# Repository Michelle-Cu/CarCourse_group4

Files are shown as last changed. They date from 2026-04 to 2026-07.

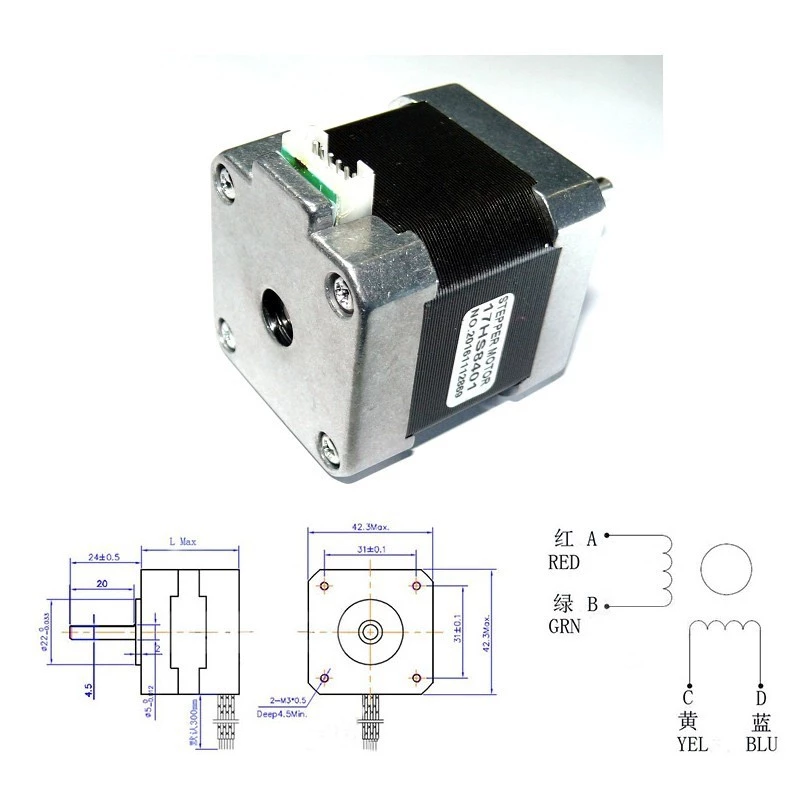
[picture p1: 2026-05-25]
SelfChosenTopic/Carinventor/Nema17圖紙.webp

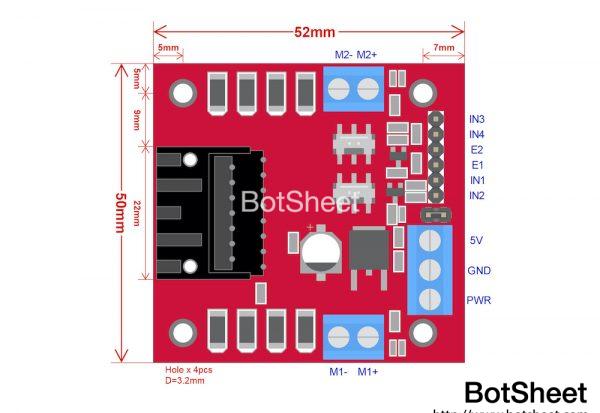
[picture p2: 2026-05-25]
SelfChosenTopic/Carinventor/l298n-motor-driver-module-dimension-600x413.jpeg

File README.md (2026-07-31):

# CarCourse_group4

## Results

Finger movements:
Robotic finger bends according to the flex sensors on the glove.
Finger movements

Punch:
Robotic arm ejects when the sensor glove's acceleration exceeds 1.5g.
Punch

Demo Video:
https://www.youtube.com/watch?v=hl6YXo5eNV0

## Project structure:

```mermaid
flowchart TB
    %% ==================== 手套端 (GLOVE SIDE) ====================
    subgraph GLOVE ["手套端感測 (Glove Controller)"]
        direction TB
        A["使用者手部動作"] --> B1["自製彎曲感測器 ×5<br/>(手指彎曲)"]
        A --> B2["MPU6050 加速度感測器<br/>(手腕姿態與速度)"]

        subgraph Flex_Proc ["手指訊號處理"]
            C1["讀取類比電壓值"] --> D1["Kalman Filter"]
            D1 --> E1["三段式角度校正"]
            E1 --> F1["映射至機器手指角度<br/>(0° ~ 180°)"]
        end

        subgraph Acc_Proc ["寸拳判定邏輯"]
            C2["讀取三軸加速度"] --> D2["計算運動加速度<br/>√(x² + y² + z²)"]
            D2 --> E2{"加速度<br/>> 1.5g (15 m/s²)?"}
            E2 -- 是 --> F2_1["設置出拳旗標 (Punch Flag = 1)"]
            E2 -- 否 --> F2_2["設置出拳旗標 (Punch Flag = 0)"]
        end

        B1 --> C1
        B2 --> C2

        F1 --> G1["資料整合與封包打包<br/>(PACKED Struct)"]
        F2_1 --> G1
        F2_2 --> G1
    end

    %% ==================== 通訊與接收 (COMMUNICATION) ====================
    G1 --->|ESP-NOW 無線通訊<br/> 6-Byte packet| H1["ESP32 接收端"]

    %% ==================== 接收端主控邏輯 (MAIN LOGIC) ====================
    subgraph MAIN_SYSTEM ["機械手臂"]
	    H1
    end

    %% ==================== 三維輸出端 (ROBOTIC HAND / ARM / AUDIO) ====================
    subgraph PALM_SYS ["手掌端 (Robotic Hand)"]
        H1 ----> K1["伺服馬達角度映射<br/>(硬體極限安全調校)"]
        K1 --> L1["寫入 5× Servo Motors"]
        L1 --> M1["驅動機械手指仿生運動"]
    end

    subgraph ARM_SYS ["手臂寸拳端 (Robotic Arm)"]
        H1 ----> K2{"出拳 flag == 1<br/>且 未處於出拳狀態<br/>且 冷卻時間 > 1秒?"}
        K2 -- 是 --> L2_1["點亮指示 LED &<br/>驅動步進馬達正轉 90°<br/>【寸拳強力彈出】"]
        K2 -- 否 --> L2_2["步進馬達保持靜態阻尼"]
        
        L2_1 --> M2_1["手臂恢復 <br/>(延遲 1 秒)"]
        M2_1 --> M2_2["驅動步進馬達正轉 270°"]
        M2_2 --> M2_3["關閉 LED &<br/>重啟 1秒冷卻計時器"]
        M2_3 --> L2_2
        
        L2_1 -.->|中斷驅動| N2["Hardware Timer ISR<br/>(高精密運動規劃)"]
        M2_2 -.->|中斷驅動| N2
        N2 --> O2["驅動 Stepper Motor"]
    end

    subgraph AUDIO_SYS ["音效端 (Audio System)"]
        H1 ----> K3["寸拳與動作動態音效觸發"]
        K3 --> L3["DFPlayer Mini 模組"]
        L3 --> M3["喇叭即時音效輸出"]
    end

    %% ==================== 視覺樣式設定 (THEMING) ====================
    style GLOVE fill:#e1f5fe,stroke:#03a9f4,stroke-width:2px,color:#000;
    style MAIN_SYSTEM fill:#fff9c4,stroke:#fbc02d,stroke-width:2px,color:#000;
    style PALM_SYS fill:#e8f5e9,stroke:#4caf50,stroke-width:2px,color:#000;
    style ARM_SYS fill:#ffe0b2,stroke:#fb8c00,stroke-width:2px,color:#000;
    style AUDIO_SYS fill:#f3e5f5,stroke:#9c27b0,stroke-width:2px,color:#000;
    
    style E2 fill:#ffe0b2,stroke:#fb8c00,stroke-width:2px,color:#000;
    style K2 fill:#ffe0b2,stroke:#fb8c00,stroke-width:2px,color:#000;
    style H1 fill:#3f51b5,stroke:#303f9f,color:#fff;
    style G1 fill:#03a9f4,stroke:#0288d1,color:#fff;
```

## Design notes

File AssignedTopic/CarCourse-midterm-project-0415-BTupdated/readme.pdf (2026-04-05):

# 電資工程入門設計與實作

# sample code講解

影片連結:https://www.youtube.com/watch?v=WLR578UgFHk

Author: B07901029陳君輔

Contact: chunfuchen0311@gmail.com

Date: 2022/07

# 檔案架構

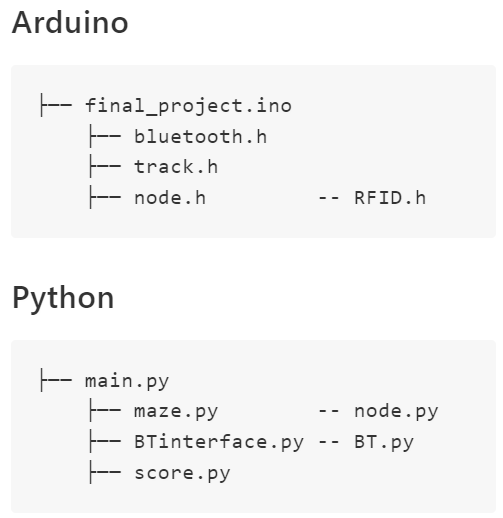
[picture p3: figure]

# Python

## Python 套件安裝

- pip install python-socketio

## score.py使用方法

- ScoreboardFake
- 使用fakeUID.csv裡的資料計分
- 使用時機: server尚未開啟 或者 server太多人在使用
- 分數不會出現在server上
- Scoreboard
- 連線到server計分 (網址以助教公布的為準)
- 使用時機: 想刷榜 或者 正式考試時
- 分數會出現在server上

除了一開始宣告的名字不一
樣之外，其他funtion使用起
來都一樣，可以無痛切換

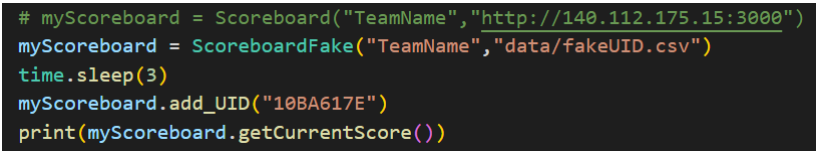
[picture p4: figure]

# Arduino

# 藍芽腳位

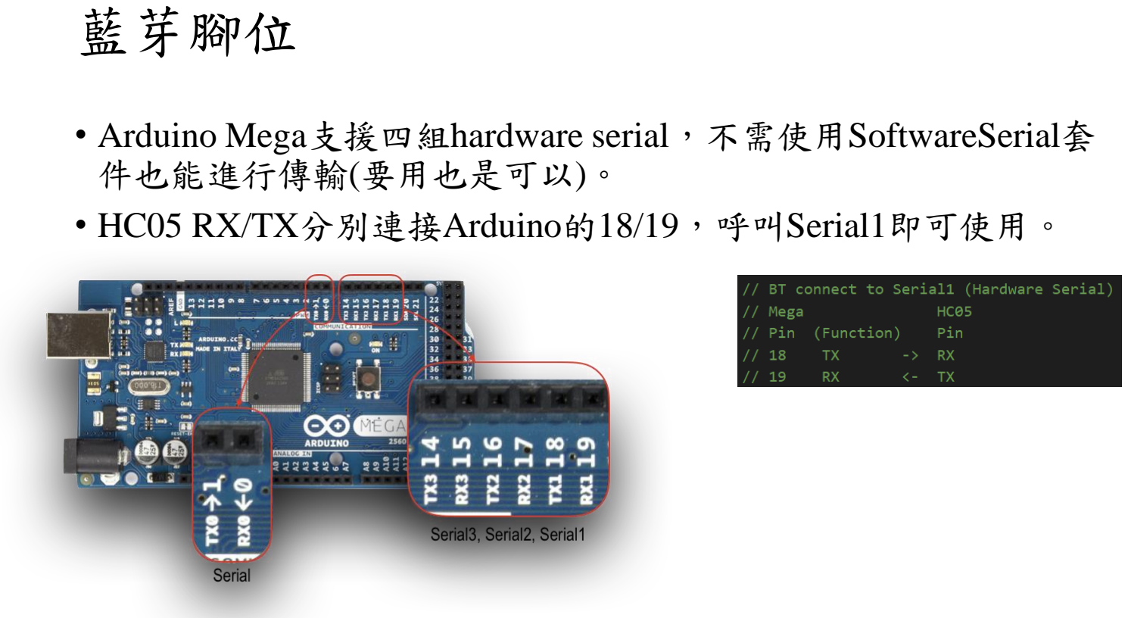
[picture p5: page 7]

- Arduino Mega支援四組hardware serial，不需使用SoftwareSerial套 件也能進行傳輸(要用也是可以)。
- HC05 RX/TX分別連接Arduino的18/19，呼叫Serial1即可使用。

## UID補零

- Arduino:
- id=[\xA2,\x04,\x56,\x7B]
- Python:

UID=“A24567B”

UID=“A204567B”

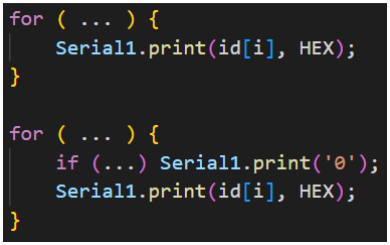
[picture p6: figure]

用BT.write就不會有補零的問題

## *補充: 藍芽傳輸(Python → Arduino)

- Python | • Arduino

bytes

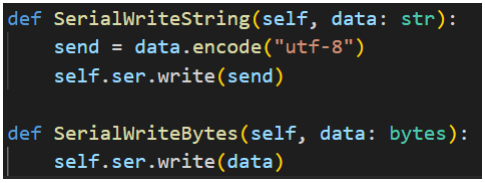
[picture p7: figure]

(str) ‘f’ | encode() | (bytes) b’\x66’ | read() | (char) ‘f’

太費時間，在Action()裡
| 可以改用bytes存

send()

## *補充: 藍芽傳輸(Arduino → Python)

- Arduino
- id=[\xA2,\x04,\x56,\x7B]
- Python
162 | 4 | 86 | 123

SerialReadString

SerialReadByte

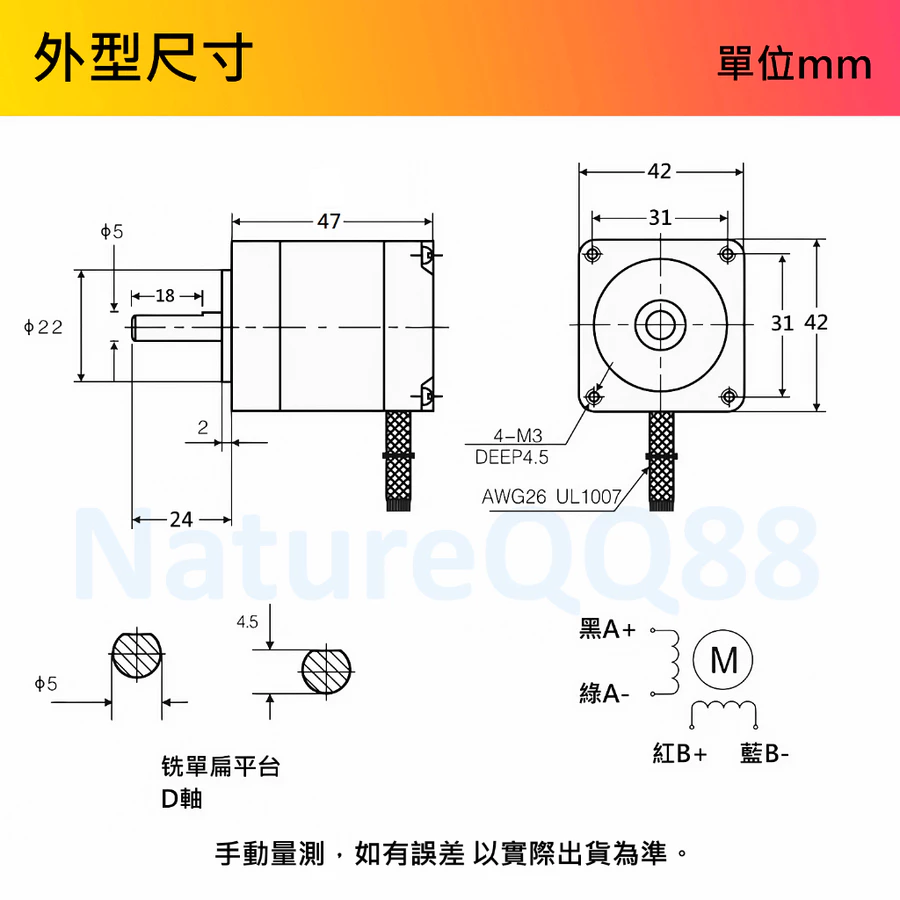
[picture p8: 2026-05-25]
SelfChosenTopic/Carinventor/Nema17withD.webp

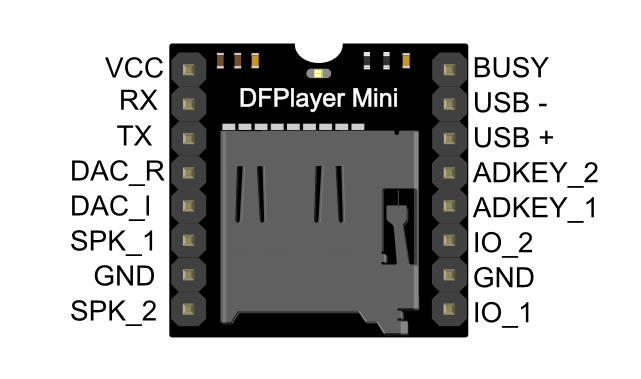
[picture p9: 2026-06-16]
SelfChosenTopic/Carinventor/mp3_module.webp

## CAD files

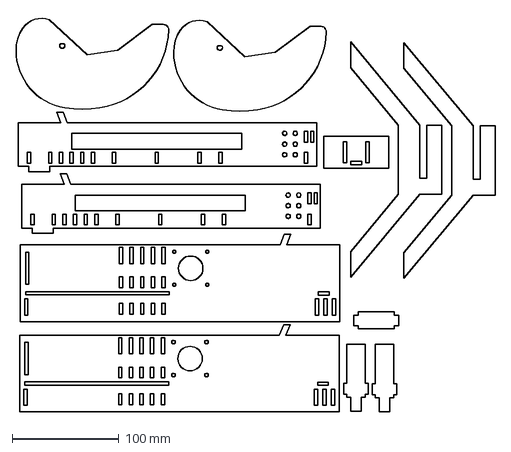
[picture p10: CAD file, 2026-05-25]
SelfChosenTopic/Carinventor/2ndmodel/Faces/Full.dxf
449.7 x 371.5 mm

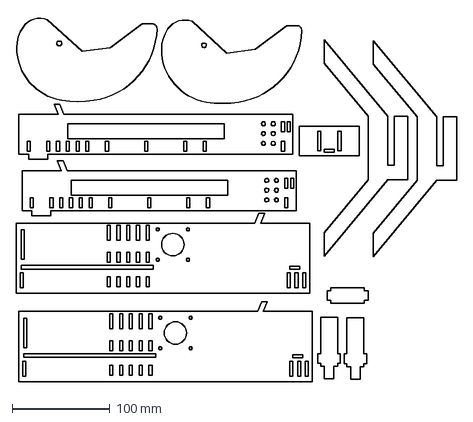
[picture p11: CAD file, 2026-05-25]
SelfChosenTopic/Carinventor/2ndmodel/Faces/Full_v2.dxf
450.3 x 373.9 mm

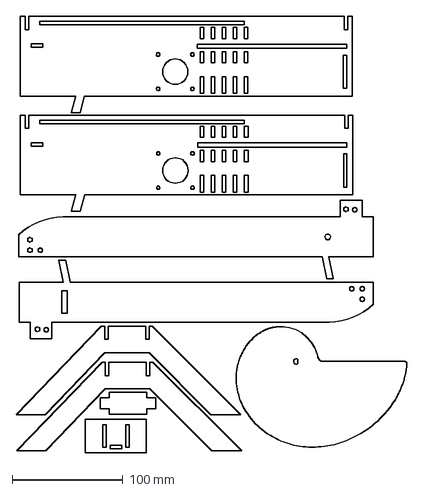
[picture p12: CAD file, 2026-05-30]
SelfChosenTopic/Carinventor/3rdmodel/faces/May25full.dxf
352.9 x 394.1 mm

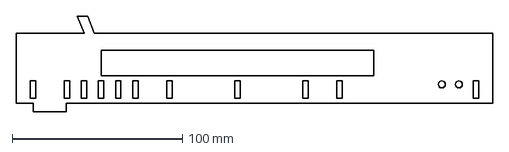
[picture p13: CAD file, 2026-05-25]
SelfChosenTopic/Carinventor/1stmodel/Faces/middle_bar.dxf
280.0 x 56.0 mm

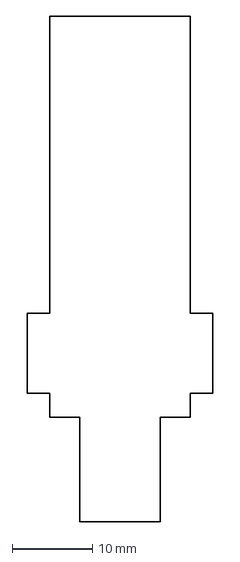
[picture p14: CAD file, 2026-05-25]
SelfChosenTopic/Carinventor/2ndmodel/Faces/Contact_board2.dxf
23.1 x 63.0 mm

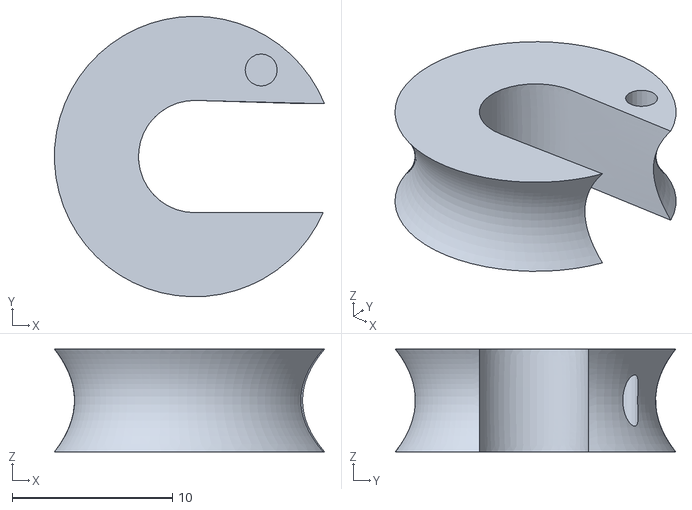
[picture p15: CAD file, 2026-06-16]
SelfChosenTopic/Carinventor/3DPs/sg90_shaft_support_v2.stl
16.8 x 17.5 x 6.40

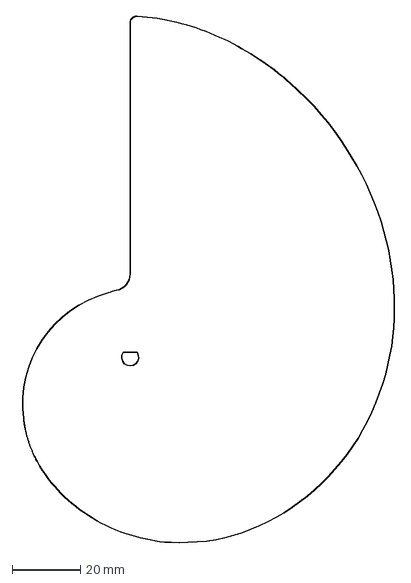
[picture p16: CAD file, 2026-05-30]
SelfChosenTopic/Carinventor/3rdmodel/faces/cam3.dxf
110.9 x 154.2 mm

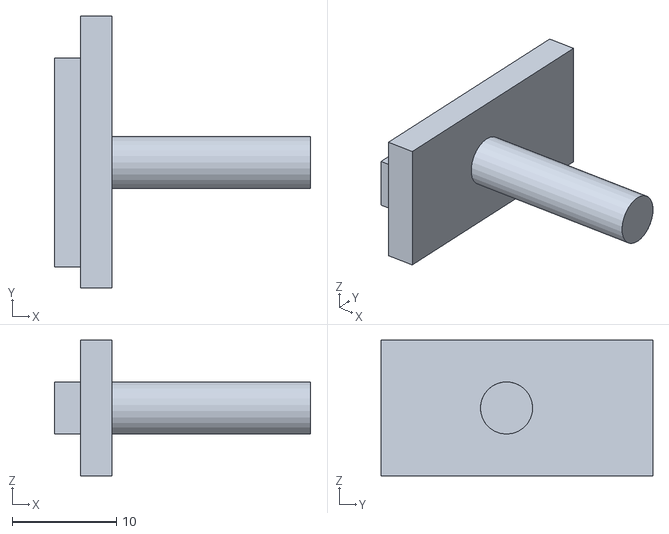
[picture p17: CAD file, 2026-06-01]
SelfChosenTopic/Carinventor/3rdmodel/stl/contact_axisv2.stl
24.5 x 26.0 x 13.0

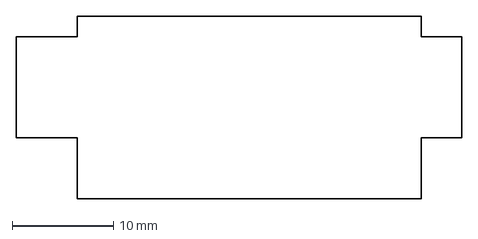
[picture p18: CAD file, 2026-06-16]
SelfChosenTopic/Carinventor/4thmodel/dwg/Frontrail_v2_p1.dxf
44.0 x 18.0 mm

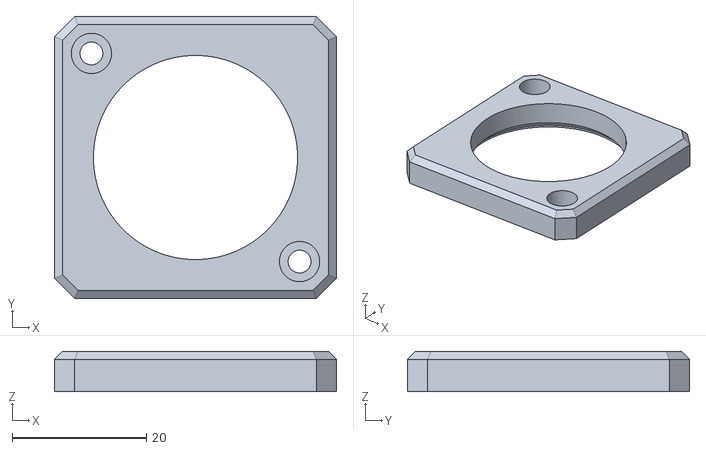
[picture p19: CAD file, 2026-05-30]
SelfChosenTopic/Carinventor/stackable-nema-17-gearbox-model_files/cap.stl
42.0 x 42.0 x 6.00

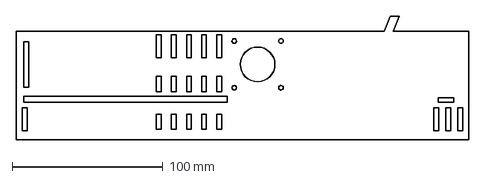
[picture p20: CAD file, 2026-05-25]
SelfChosenTopic/Carinventor/2ndmodel/Faces/Sideboard2.dxf
300.0 x 82.0 mm

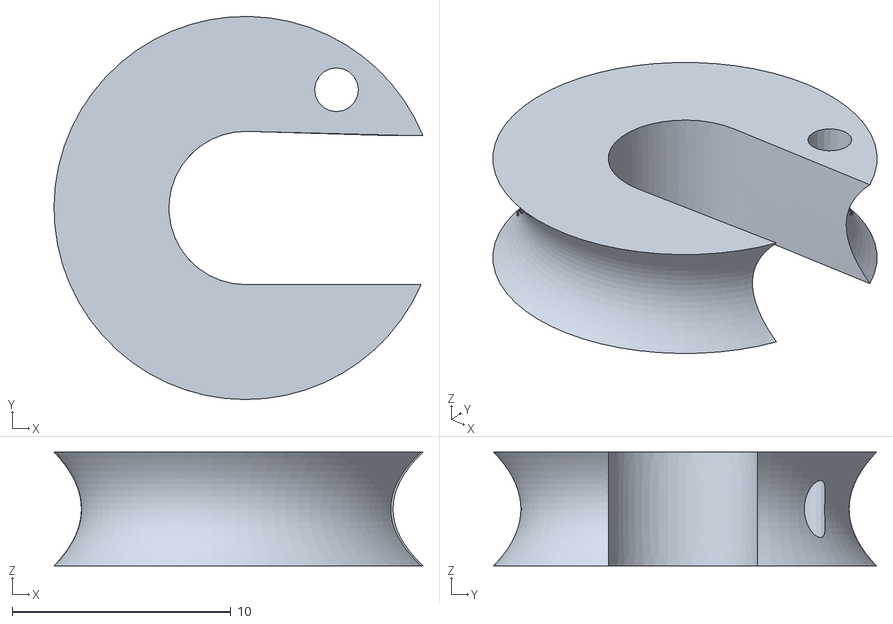
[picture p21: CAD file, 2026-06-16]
SelfChosenTopic/Carinventor/3DPs/sg90_shaft_support.stl
16.9 x 17.5 x 5.20

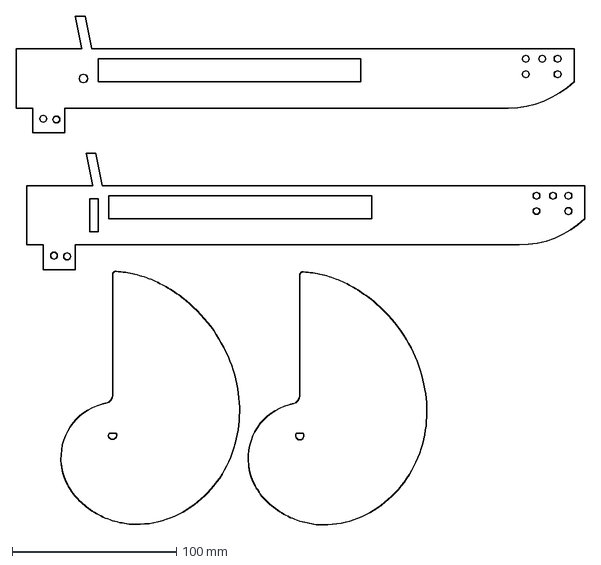
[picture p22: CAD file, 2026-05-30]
SelfChosenTopic/Carinventor/3rdmodel/faces/May25print2.dxf
346.5 x 310.0 mm

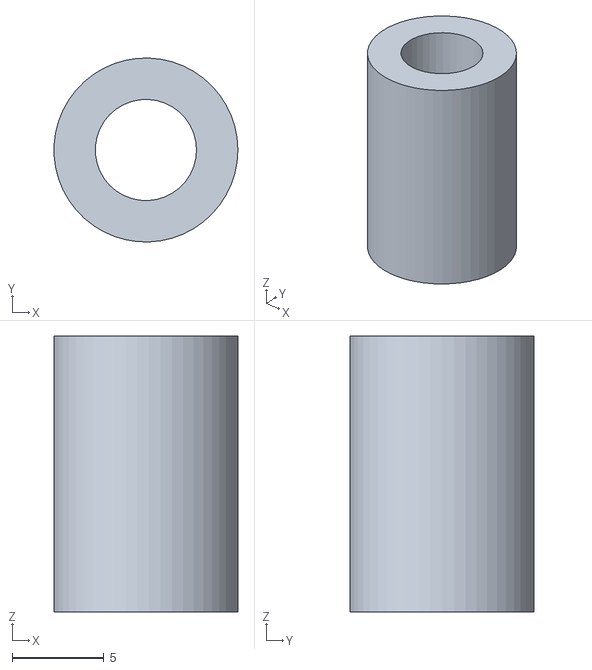
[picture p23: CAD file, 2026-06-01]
SelfChosenTopic/Carinventor/3rdmodel/stl/contact_axis_outerv2.stl
9.99 x 9.99 x 15.0

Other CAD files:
SelfChosenTopic/Carinventor/4thmodel/dwg/Back_board_p1.dxf
SelfChosenTopic/Carinventor/stackable-nema-17-gearbox-model_files/keyedoutput.stl
SelfChosenTopic/Carinventor/3rdmodel/faces/Cam.dxf
SelfChosenTopic/Carinventor/3rdmodel/stl/Cam_archi1.stl
SelfChosenTopic/Carinventor/1stmodel/Assembly1.iam
SelfChosenTopic/Carinventor/1stmodel/Assembly2.iam
SelfChosenTopic/Carinventor/1stmodel/Assembly3-2.iam
SelfChosenTopic/Carinventor/1stmodel/Assembly3.iam
SelfChosenTopic/Carinventor/1stmodel/Backboard.ipt
SelfChosenTopic/Carinventor/1stmodel/D_coupler.ipt
SelfChosenTopic/Carinventor/1stmodel/Frontrail.ipt
SelfChosenTopic/Carinventor/1stmodel/Middle_bar.ipt
SelfChosenTopic/Carinventor/1stmodel/Middle_bar3.ipt
SelfChosenTopic/Carinventor/1stmodel/Moving_rail.ipt
SelfChosenTopic/Carinventor/1stmodel/Moving_rail3.ipt
SelfChosenTopic/Carinventor/1stmodel/Moving_rail_wide.ipt
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

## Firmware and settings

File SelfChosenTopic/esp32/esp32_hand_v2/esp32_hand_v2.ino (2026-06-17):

#include <esp_now.h>

#include <WiFi.h>
#include <ESP32Servo.h>
#include "esp_mac.h"
#include "DFRobotDFPlayerMini.h" 

// Pin Definitions
const int servoPins[5] = {32, 33, 25, 26, 27};
const int stepPin = 14;
const int dirPin = 13; 
const int bootButton = 0; 
const int ledPin = 2;     

// === AUDIO PIN DEFINITIONS ===
#define ESP32_RX_PIN 16  // Connects to DFPlayer TX
#define ESP32_TX_PIN 17  // Connects to DFPlayer RX
HardwareSerial dfPlayerSerial(2); 
DFRobotDFPlayerMini myDFPlayer;

// Hardware Timer for Stepper Polling
hw_timer_t * stepperTimer = NULL;

// Stepper control variables
volatile long stepperRemainingSteps = 0;
const int punchDirection = LOW; 

// Helper to set/change timer alarm interval and start the timer
void setTimerInterval(uint32_t intervalUs) {
  if (stepperTimer == NULL) return;
#if ESP_ARDUINO_VERSION >= ESP_ARDUINO_VERSION_VAL(3, 0, 0)
  timerAlarm(stepperTimer, intervalUs, true, 0);
  timerStart(stepperTimer);
#else
  timerAlarmWrite(stepperTimer, intervalUs, true);
  timerAlarmEnable(stepperTimer);
#endif
}

// Helper to stop the timer
void stopTimer() {
  if (stepperTimer == NULL) return;
#if ESP_ARDUINO_VERSION >= ESP_ARDUINO_VERSION_VAL(3, 0, 0)
  timerStop(stepperTimer);
#else
  timerAlarmDisable(stepperTimer);
#endif
}

// IRAM-safe hardware timer ISR for generating step pulses
void IRAM_ATTR onStepperTimer() {
  if (stepperRemainingSteps > 0) {
    digitalWrite(stepPin, HIGH);
    ets_delay_us(10); 
    digitalWrite(stepPin, LOW);
    stepperRemainingSteps--;
    if (stepperRemainingSteps == 0) {
#if ESP_ARDUINO_VERSION >= ESP_ARDUINO_VERSION_VAL(3, 0, 0)
      timerStop(stepperTimer);
#else
      timerAlarmDisable(stepperTimer);
#endif
    }
  }
}

// Punch Stepper Settings
const int stepsPerRotation = 1600; 
const float punchAngle = 90.0;     
const float rechargeAngle = 270.0; 
const float punchSpeed = 400.0;    
const float rechargeSpeed = 400.0; 
const int punchPauseMs = 1000;     

// Servos
Servo servos[5];

// Data structure to receive
typedef struct struct_message {
  uint8_t finger_angles[5];
  uint8_t trigger_punch; 
} __attribute__((packed)) struct_message;

struct_message myData;
volatile bool dataReady = false; 
volatile unsigned long lastRecvTime = 0;

// Punch settings
bool isPunching = false;
unsigned long lastPunchEndTime = 0;
const unsigned long punchCooldownMs = 1000; 

unsigned long lastSoundTime = 0;  //Sound settings
bool straight[5];

// === 1-BASED ENUM MODIFICATION ===
enum PunchState {
  PUNCH_IDLE = 1,       // 1
  PUNCH_EXTENDING,      // 2
  PUNCH_PAUSED,         // 3
  PUNCH_RECHARGING      // 4
};
PunchState punchState = PUNCH_IDLE; // Starts tracking at 1
unsigned long punchPauseStartTime = 0;

void gestureSound(){
  if( millis() - lastSoundTime < 2000) return; 
  int count = 0;
  for (int i = 0; i < 5; i++) {
      int rawAngle = myData.finger_angles[i];
      if( rawAngle < 90 ) {straight[i] = 1; count++; }
      else{ straight[i] = 0; }
      Serial.print(straight[i]);
      Serial.print(" ");
  }
  Serial.println(count);
  if( straight[0] == 1 && straight[4] == 1 && count == 2) { myDFPlayer.play(6); lastSoundTime = millis();}              //six
  else if( straight[0] == 1 && straight[1] == 1 && count == 2) { myDFPlayer.play(5); lastSoundTime = millis();}           //seven
  else if( straight[1] == 1 && straight[2] == 1 && straight[3] == 1 && count == 3) { myDFPlayer.play(3); lastSoundTime = millis();}   //three
  else if( count == 0) { myDFPlayer.play(4); lastSoundTime = millis();}         //18hand
}

void triggerPunch() {
  if (punchState == PUNCH_IDLE) {
    punchState = PUNCH_EXTENDING; // Changes state to 2
    isPunching = true;
    Serial.println("PUNCH TRIGGERED!");
    digitalWrite(ledPin, HIGH); 
    
    // Play punch sound (0001.mp3)
    myDFPlayer.play(1); 
    lastSoundTime = millis();
    
    // 1. Punch Stroke (90 degrees)
    long stepsPunch = (long)((punchAngle / 360.0) * stepsPerRotation);
    digitalWrite(dirPin, punchDirection);
    
    uint32_t stepIntervalUs = (uint32_t)(1000000.0 / punchSpeed);
    
    stepperRemainingSteps = stepsPunch;
    setTimerInterval(stepIntervalUs);
  }
}

void updatePunch() {
  switch (punchState) {
    case PUNCH_IDLE: // Case 1
      break;
      
    case PUNCH_EXTENDING: // Case 2
      if (stepperRemainingSteps == 0) {
        punchState = PUNCH_PAUSED; // Changes state to 3
        punchPauseStartTime = millis();
      }
      break;
      
    case PUNCH_PAUSED: // Case 3
      if (millis() - punchPauseStartTime >= punchPauseMs) {
        punchState = PUNCH_RECHARGING; // Changes state to 4
        long stepsRecharge = (long)((rechargeAngle / 360.0) * stepsPerRotation);
        
        digitalWrite(dirPin, punchDirection); 
        
        // Play recharge sound (0004.mp3)
        myDFPlayer.play(2);
        lastSoundTime = millis();
        
        uint32_t stepIntervalUs = (uint32_t)(1000000.0 / rechargeSpeed);
        
        stepperRemainingSteps = stepsRecharge;
        setTimerInterval(stepIntervalUs);
      }
      break;
      
    case PUNCH_RECHARGING: // Case 4
      if (stepperRemainingSteps == 0) {
        digitalWrite(ledPin, LOW); 
        punchState = PUNCH_IDLE; // Returns back to 1
        isPunching = false;
        lastPunchEndTime = millis(); 
      }
      break;
  }
}

// ESP-NOW CALLBACK
#if ESP_ARDUINO_VERSION >= ESP_ARDUINO_VERSION_VAL(3, 0, 0)
void OnDataRecv(const esp_now_recv_info_t *recv_info, const uint8_t *incomingData, int len) {
  if (len == sizeof(struct_message)) {
    memcpy(&myData, incomingData, sizeof(myData));
    dataReady = true;
    lastRecvTime = millis();
  }
}
#else
void OnDataRecv(const uint8_t * mac, const uint8_t *incomingData, int len) {
  if (len == sizeof(struct_message)) {
    memcpy(&myData, incomingData, sizeof(myData));
    dataReady = true;
    lastRecvTime = millis();
  }
}
#endif

void setup() {
  Serial.begin(115200);
  delay(1000);
  Serial.println("\n--- ESP32 HAND START WITH 1-BASED ENUM ---");

  // Initialize Audio Serial
  dfPlayerSerial.begin(9600, SERIAL_8N1, ESP32_RX_PIN, ESP32_TX_PIN);
  if (!myDFPlayer.begin(dfPlayerSerial)) {
    Serial.println("Warning: DFPlayer Mini not detected! Check wiring/SD card.");
  } else {
    Serial.println("DFPlayer Mini online and ready.");
    myDFPlayer.volume(28); 
  }

  WiFi.mode(WIFI_STA);
  if (esp_now_init() != ESP_OK) {
    Serial.println("Error initializing ESP-NOW");
    return;
  }
  esp_now_register_recv_cb(OnDataRecv);

  ESP32PWM::allocateTimer(0);
  ESP32PWM::allocateTimer(1);
  ESP32PWM::allocateTimer(2);
  ESP32PWM::allocateTimer(3);

  for (int i = 0; i < 5; i++) {
    servos[i].setPeriodHertz(50);
    servos[i].attach(servoPins[i], 500, 2500); 
    servos[i].write(0);
  }
  pinMode(stepPin, OUTPUT);
  pinMode(dirPin, OUTPUT);
  pinMode(ledPin, OUTPUT);
  digitalWrite(ledPin, LOW); 
  pinMode(bootButton, INPUT_PULLUP); 

#if ESP_ARDUINO_VERSION >= ESP_ARDUINO_VERSION_VAL(3, 0, 0)
  stepperTimer = timerBegin(1000000); 
  timerAttachInterrupt(stepperTimer, &onStepperTimer);
#else
  stepperTimer = timerBegin(0, 80, true); 
  timerAttachInterrupt(stepperTimer, &onStepperTimer, true);
#endif 

  Serial.println("Ready.");
}

void loop() {
  updatePunch();

  if (digitalRead(bootButton) == LOW && !isPunching && (millis() - lastPunchEndTime >= punchCooldownMs)) {
    triggerPunch();
  }

  if (dataReady) {
    dataReady = false; 

    // Move Servos 
    static int lastServoAngles[5] = {-1, -1, -1, -1, -1};
    for (int i = 0; i < 5; i++) {
      int rawAngle = myData.finger_angles[i];

      if (rawAngle != lastServoAngles[i]) {
        servos[i].write(rawAngle);
        lastServoAngles[i] = rawAngle;
      }
    }

    

    // Punch Check from Glove Transmissions
    if (myData.trigger_punch == 1 && !isPunching && (millis() - lastPunchEndTime >= punchCooldownMs)) {
      triggerPunch();
    }
    else if (!isPunching) {
      gestureSound(); // Only trigger gesture sounds when not punching
    }
  }
  yield(); 
}

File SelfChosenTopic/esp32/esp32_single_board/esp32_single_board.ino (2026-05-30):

/*
  ESP32 Single Board Integrated Controller (Robotic Arm Glove + Hand)
  
  This sketch integrates the MPU-6050 IMU, 5x Carbon Flex Sensors, 
  5x Servos, and 1x A4988 Stepper Motor onto a single ESP32 board.
  ESP-NOW communication has been removed.
  
  PIN CONFLICT RESOLUTION:
  - Glove originally used:
      Flex pins: 34, 35, 36, 39, 32
  - Hand originally used:
      Servo pins: 12, 13, 14, 25, 27
      Stepper pins: step=32, dir=33
  - Pin 32 was shared between the 5th flex sensor and the stepper step pin.
  - To make all 7 actuator pins contiguous on one side of the ESP32 (GPIO 32, 33, 25, 26, 27, 14, 12):
      We moved the 5th flex sensor pin to GPIO 13 (ADC2_CH4) to avoid conflict with Servo 0 (GPIO 32).
      Since Wi-Fi/ESP-NOW is disabled, ADC2 pins can be used for analog reads.
*/

#include <Adafruit_MPU6050.h>
#include <Adafruit_Sensor.h>
#include <Wire.h>
#include <Preferences.h>
#include <ESP32Servo.h>

// Pin Definitions
// Flex Sensors (Analog Inputs)
const int flexPins[5] = {34, 35, 36, 39, 13}; // Pin 13 avoids conflict with Servo 0 (GPIO 32) and Servo 1 (GPIO 33)
const int bootButton = 0;                      // Used to trigger calibration

// Actuators
const int servoPins[5] = {32, 33, 25, 26, 27};
const int stepPin = 14;
const int dirPin = 12;

// Servos
Servo servos[5];

// Servo mapping ranges (finger angle 0-180 maps to servoMin-servoMax)
const int servoMinAngles[5] = {0, 0, 30, 10, 30};
const int servoMaxAngles[5] = {180, 180, 180, 180, 180};

// MPU6050
Adafruit_MPU6050 mpu;
Preferences preferences;

// Calibration Data
struct CalibrationData {
  int openVal;
  int halfVal;
  int closedVal;
};
CalibrationData fingerCal[5];

// Current State
uint8_t finger_angles[5] = {0, 0, 0, 0, 0};
float x_acceleration = 0.0;

// Manual override settings for Serial control
bool manualMode = false;
uint8_t manual_angles[5] = {0, 0, 0, 0, 0};

// Punch settings
const float accelerationThreshold = 9.81; // 1.0g in m/s^2 (1.0 * 9.81)
bool isPunching = false;
bool mpuPresent = false;

void saveCalibration() {
  preferences.begin("flex-cal", false);
  for (int i = 0; i < 5; i++) {
    String key = "f" + String(i);
    preferences.putInt((key + "o").c_str(), fingerCal[i].openVal);
    preferences.putInt((key + "h").c_str(), fingerCal[i].halfVal);
    preferences.putInt((key + "c").c_str(), fingerCal[i].closedVal);
  }
  preferences.end();
  Serial.println("Calibration saved to NVS.");
}

void loadCalibration() {
  preferences.begin("flex-cal", true);
  for (int i = 0; i < 5; i++) {
    String key = "f" + String(i);
    fingerCal[i].openVal = preferences.getInt((key + "o").c_str(), 2000);
    fingerCal[i].halfVal = preferences.getInt((key + "h").c_str(), 2500);
    fingerCal[i].closedVal = preferences.getInt((key + "c").c_str(), 3000);
  }
  preferences.end();
  Serial.println("Calibration loaded from NVS.");
}

void runCalibration() {
  Serial.println("\n=== STARTING CALIBRATION ===");
  const char* labels[3] = {"FULLY OPEN", "HALF CLOSED", "FULLY CLOSED"};

  for (int p = 0; p < 3; p++) {
    Serial.print("\nPosition: "); Serial.println(labels[p]);
    Serial.println("Hold position and press BOOT button...");
    
    // Wait for press
    while (digitalRead(bootButton) == HIGH) delay(10);
    delay(500); // Debounce
    
    // Read values
    for (int i = 0; i < 5; i++) {
      int val = analogRead(flexPins[i]);
      if (p == 0) fingerCal[i].openVal = val;
      else if (p == 1) fingerCal[i].halfVal = val;
      else fingerCal[i].closedVal = val;
      Serial.print("F"); Serial.print(i); Serial.print(": "); Serial.println(val);
    }
    
    // Wait for release
    while (digitalRead(bootButton) == LOW) delay(10);
    delay(500);
  }
  saveCalibration();
  Serial.println("=== CALIBRATION COMPLETE ===\n");
}

uint8_t mapFlex(int val, CalibrationData cal) {
  float angle;
  // Segment 1: Open to Half
  if ((cal.openVal < cal.closedVal && val <= cal.halfVal) || (cal.openVal > cal.closedVal && val >= cal.halfVal)) {
    angle = map(val, cal.openVal, cal.halfVal, 0, 90);
  } else {
    angle = map(val, cal.halfVal, cal.closedVal, 90, 180);
  }
  return (uint8_t)constrain(angle, 0, 180);
}

void triggerPunch() {
  isPunching = true;
  Serial.println("PUNCH TRIGGERED!");
  digitalWrite(dirPin, HIGH);
  for (int i = 0; i < 200; i++) {
    digitalWrite(stepPin, HIGH);
    delayMicroseconds(500);
    digitalWrite(stepPin, LOW);
    delayMicroseconds(500);
  }
  delay(500);
  digitalWrite(dirPin, LOW);
  for (int i = 0; i < 200; i++) {
    digitalWrite(stepPin, HIGH);
    delayMicroseconds(2000);
    digitalWrite(stepPin, LOW);
    delayMicroseconds(2000);
  }
  isPunching = false;
}
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

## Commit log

2026-03-16 bluetooth arduino test code
2026-03-23 add esp32 BT Bridge
2026-03-23 temporalily working on millis() and cycle control
2026-03-23 PID tracking
2026-03-28 not performing avg time claculation on arduino
2026-03-29 cross tracking yet to be done, bluetooth monitoring yet to be tested (fixed baud rate and message inconsistency
    [robot_data_20260328_115505.csv]
2026-03-30 fix BT connection issue
    [robot_data_20260328_115505.csv, robot_data_20260330_142406.csv, robot_data_20260330_143355.csv]
2026-03-30 BT messgae sending freqeuncy reduce to 10 for stability, IR reading frequency can now be higher up to 100. (Yet to be tested, BT connection still not stable)
    [mar30_CrossAndRemoteMonitor.ino]
2026-03-31 integrated the pid code and crossline tracing. not tested yet.
2026-04-03 fix BT connection problem & flashing bluetooth configuration to my esp32
    [mar30_CrossAndRemoteMonitor.ino]
2026-04-05 midterm project edited from sample code. Can connect to server and run FakeUIDs
    [0404maze.csv, fakeUID.csv, small_maze.csv]
2026-04-06 Arduino, BFS, BT integrated
    [0404maze.csv, cross.csv, fakeUID.csv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]
2026-04-07 fix: bluetooth connection problem. delete: data tranfering and logging (reason: shouldn't be a big deal)
    [April4th_remote.ino, hm10_esp32_bridge.py, hm10_esp32_bridge_original.py]
2026-04-18 updated BT and arduino
    [0404maze.csv, cross.csv, fakeUID.csv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]
2026-04-18 treasure counting
    [maze.csv]
2026-04-21 working BT, rfid problems fixing in progress
    [April4th_integrated.ino, bluetooth.h, main.py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]
2026-04-21 shortest path implemented as mode 1, moves self testing mode to mode 2
    [main.py, midterm_project.ino]
2026-04-22 add sequence_to_directions file
    [big_maze_114.csv]
2026-04-23 add: medium_maze.csv, gitignore, modified: bt sync logic (TESTING NEEDED)
    [medium_maze.csv]
2026-05-11 add: make folders for past assigned topic and for future chosen topic
    [0404maze.csv, big_maze_114.csv, cross.csv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]
2026-05-11 add: ble connection sample test files for esp32 and raspberry pi
2026-05-18 refine codebase for dual esp32 board
2026-05-19 voltage tester
2026-05-24 inventor added
    [Assembly1st.0009.iam, Assembly1st.iam, Assembly2.0005.iam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]
2026-05-24 working on arm v2
    [Assembly3-2.0027.iam, Assembly3-2.iam, Back_board.ipt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]
2026-05-25 v2 almost done
    [Assembly3-2.0027.iam, Assembly3-2.0030.iam, Assembly3-2.iam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]
2026-05-25 debug attempt
    [Assembly3-2.iam, Assembly3.0034.iam, Assembly3.iam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]
2026-05-30 may print 2
2026-06-01 feat: implement ESP-NOW communication system for glove sensor and robotic hand control
2026-06-02 design place for boards
    [2ndSideboard.0008.ipt, 2ndSideboard.0017.ipt, 2ndSideboard.ipt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]
2026-06-03 3rd print version
    [2ndSideboard.0017.ipt, 2ndSideboard.0024.ipt, 2ndSideboard.ipt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]
2026-06-06 forgot to print one piece
    [June6th.dxf, TB6600 holder.dxf]
2026-06-14 optimized for non jitter stepper
    [esp32_sensor.ino, sketch_jun1a.ino]
2026-06-14 add single calibration
2026-06-14 minor adjustments
    [Assembly3-2.0026.iam, Assembly3-2.0027.iam, Assembly3-2.iam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]
2026-06-15 stepper driver hardware timer
2026-06-15 reformat msg format for sensor.ino
2026-06-15 reversed rotation for stepper motor
2026-06-15 3dp U-shaft
    [sg90_shaft_support.0002.ipt, sg90_shaft_support.ipt, sg90_shaft_support.stl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]
2026-06-16 correct pin for sound module
    [sound_mod.ino]
2026-06-17 add kalman filter
